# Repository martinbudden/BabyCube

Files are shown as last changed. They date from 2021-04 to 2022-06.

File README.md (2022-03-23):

# BabyCube

The **BabyCube** is a small 3D-printed CoreXY 3D printer with a linear rails motion system.

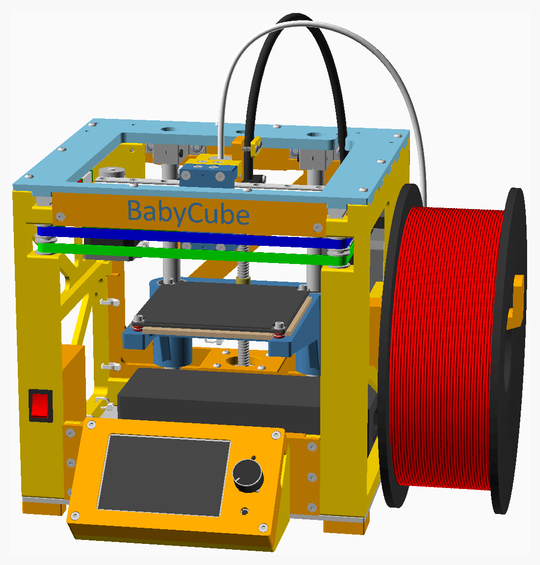
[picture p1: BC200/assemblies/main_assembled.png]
Main Assembly


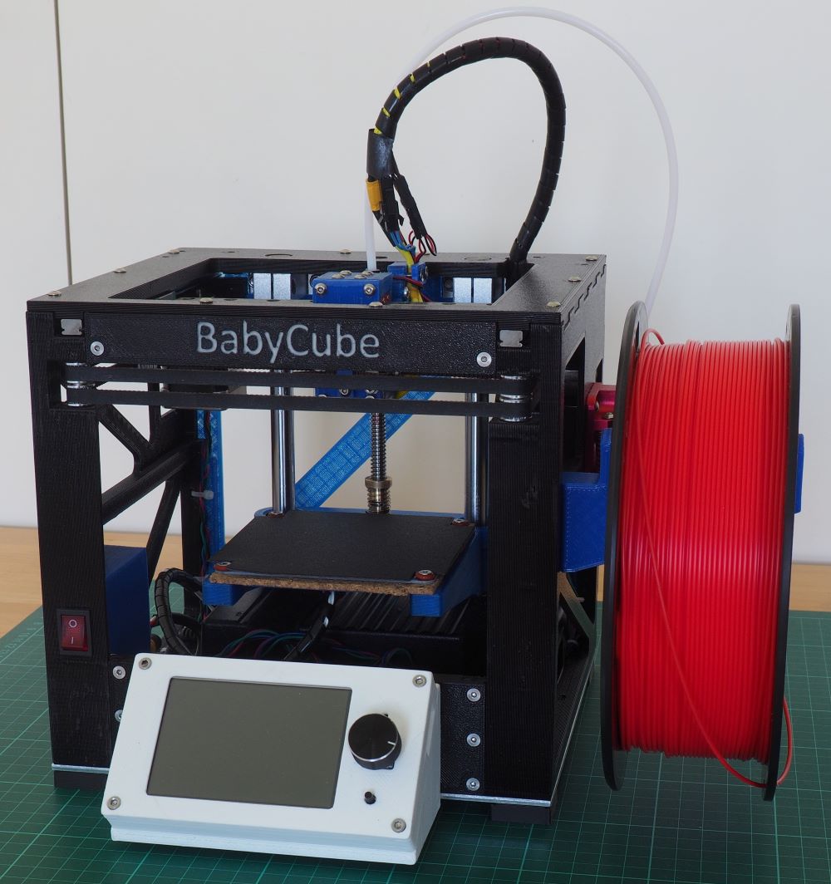
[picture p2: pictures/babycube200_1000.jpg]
BabyCube


The BabyCube has a print volume of just over 90mm by 80mm by 60mm.

The BOM cost is approximately £290 with a genuine E3D hotend (or about £250 with a generic E3D compatible hotend), this does not include the cost of filament for printing parts, see [spreadsheet](documents/BabyCube200_BOM.ods). Price is current for May 2021.

The dimensions of the cube are 220mm by 204mm by 203mm, and the enclosing volume (including the display, extruder,
and feet, but excluding the spool holder, Bowden tube and hotend wiring) is about 248mm by 272mm by 211mm.

Although the BabyCube is small and has a 3D printed frame, it is not a toy. It is an engineered machine capable of producing high quality prints.

## Assembly instructions

The assembly instructions and the BOM (parts list) are [here](BC200/readme.md). Please read all the build instructions before you begin assembly.

The STL files are on [thingiverse](https://www.thingiverse.com/thing:4911835).

A video overview of the features of BabyCube is [here](https://www.youtube.com/watch?v=HpjnHnVyvj4).

I plan to make a series of YouTube videos giving build instructions, when I have done so I will post a link here.

If you would like to build a bigger printer, you may be interested in the BabyCube's larger sibling, the [MaybeCube](https://github.com/martinbudden/MaybeCube)

## Key Features

1. Small portable quality CoreXY 3D printer with all parts integrated inside the frame (no external power brick)
2. Capable of printing high quality prints
3. Linear rails and NEMA 14 stepper motors used for CoreXY motion system
4. NEMA 17 stepper motors used for the extruder and the Z axis
5. Quiet operation
6. Sensorless homing on all axes

## Design Goals

The primary design goal was to produce a small 3D printer with a printable frame, external dimensions of approximately
200mm by 200mm by 200mm, and a target print volume of approximately 75mm by 75mm by 75mm.

The aim was that BabyCube could be printed on "standard" size printers, that is printers with a bed size of approximately 220mm by 220mm, such as the Ender 3 (print volume 220mm by 220mm by 250mm) and the Prusa i3 (print volume 250mm by 210mm by 210mm).

I printed my BabyCube on a BIQU B1 (which is similar to an Ender 3).

Further design goals:

1. **Make a 3D printer capable of producing high quality parts**
    * Ensure that the frame, even though 3D printed, is highly rigid
    * Use high quality components, including hotend, extruder, control boards etc
2. **Integrated design, with everything is enclosed within the printer's frame**
    * This includes the motors, the motion system, the power supply, and the circuit boards. The only exceptions are the extruder, the spool holder, the display and the connections to the hotend (wiring and Bowden tube).
    * all protrusions from frame (filament spool, extruder, power connector) are on the right hand side to minimise desk clutter and allow the back of the BabyCube to be pushed right against a wall
    * Clean wiring. Include the wiring in the design, rather than add it as an afterthought.
3. **Require minimal tools for assembly**
    * Assembly can essentially be completed using just hex keys.
    * Use self tapping holes rather than threaded inserts, they are just as strong - see [CNC Kitchen's video](https://www.youtube.com/watch?v=iR6OBlSzp7I)
    * Some small files are useful cleaning up printed parts, and optionally an M3 tap (and tap wrench) can be used to start self-tapping holes.
    * A drill with 2mm and 3mm bits is required to drill the holes in the aluminium base, but a 3D printed base can be used instead.
4. **Require minimal rework of printed parts**
    * [NopSCADlib](https://github.com/nophead/NopSCADlib) provides several features to avoid part rework.
    * All parts can be printed without supports. [Hanging holes](https://hydraraptor.blogspot.com/2014/03/buried-nuts-and-hanging-holes.html) are used to avoid supports in the display housing and the X_Carriage front.
    * Bolt holes are created using [horizontal holes](https://hydraraptor.blogspot.com/2020/07/horiholes-2.html) and [polyholes](https://hydraraptor.blogspot.com/2011/02/polyholes.html) and so are correct size and should not need redrilling.
5. **Use linear rails for the x and y axes**
    * linear rails are now not much more expensive than linear rods
    * linear rails make design and assembly easier, reducing the need for custom printed parts
    * linear rails allow a more compact design than linear rods
    * linear rods are used for the z-axis, since linear rails offer no advantage here
6. **Make the BabyCube as silent a possible**
    * Use TMC 2209 silent stepper drivers
    * The hotend fan is temperature regulated and only switches on when the hotend reaches 50&deg; Celsius
    * The the control board and stepper drivers are passively cooled by being thermally connected to the aluminium base (if either the BTT SKR E3 mini V2 or the BTT E3 turbo control boards are used).
    * The PSU is a fanless "brick" style laptop PSU.
7. **Try and keep the costs down**
    * the aim is not to be as cheap as possible, but rather to avoid unnecessary costs
    * use standard parts as far as possible
8. **Enable a variant with a carbon fiber frame**
    * see proof of concept [here](concepts/readme.md) (still a work in progress)
9. **Facilitate customisation and experimentation**
    * Open source design
    * Parametric design in [OpenSCAD](https://openscad.org/)
    * As far as possible, make it easy to partially disassemble the frame and exchange parts
10. **Support different size and material variants**
    * BabyCube's parametric design allows different size variants
11. **Be delightful**
    * A good design should have aspects that the user finds delightful

## Variants

The standard variant of the BabyCube uses and OpenBuilds 100 x 100 mm heated bed, however it is also possible to use a 120 x 120 x 6 mm aluminium tooling plate with a heating pad, see [printbed 120](PRINTBED120/readme.md).

The standard variant uses a BigTreeTech SKR Mini E3 v2.0 controller, however it is also possible to use the BigTreeTech SKR v1.4 (and Turbo) and BigTreeTech E3 Turbo controllers.

The standard variant uses an E3D v6 hotend, but other groovemount based hotends could be used.

The standard variant uses a BigTreeTech TFT35 v3.0 display, however it should also be possible to produce "headless" variants:

* if you use the SKR v1.4 or the SKR E3 turbo controller you can install the RepRap firmware and dispense with the display.
* you can install Klipper firmware and use a Raspberry Pi.

I have started to look at developing a variant with a carbon fiber frame, however this is very much a [work in progress](concepts/readme.md).

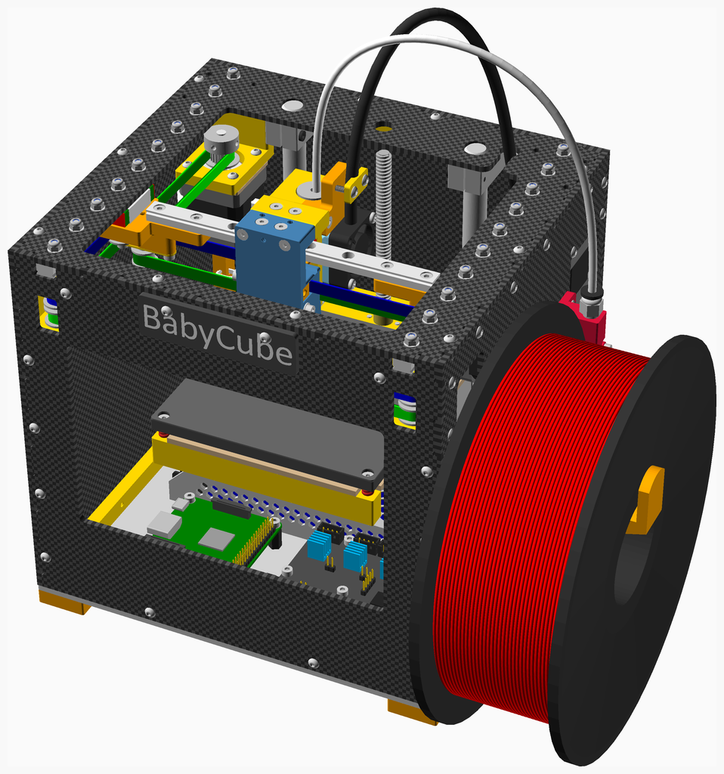
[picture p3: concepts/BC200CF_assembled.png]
BabyCubeCF


The exploded version:

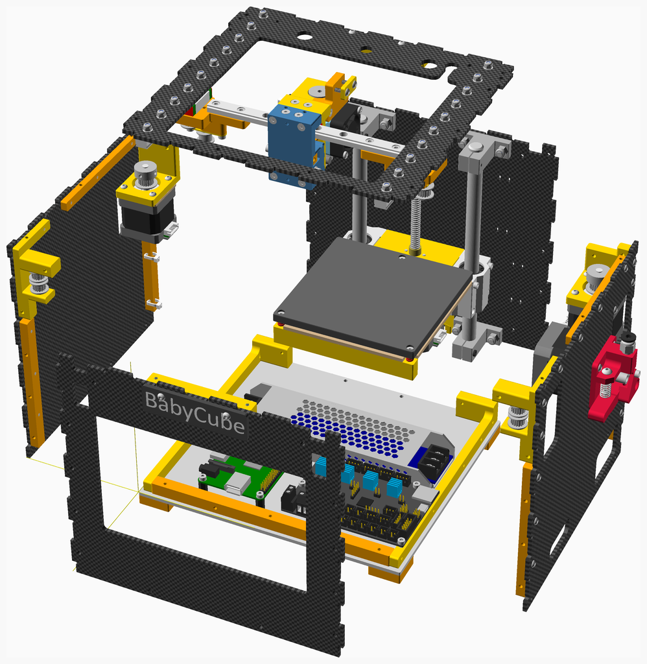
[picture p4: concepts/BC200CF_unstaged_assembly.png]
BabyCubeCF exploded


## Comparisons

The following table compares the sizes and build volumes of various small 3D printers.

Printer           | Build Volume | Nominal Dimensions
------------------| -------------| -------------------
BabyCube          | 90 x 80 x 60 | 200 x 220 x 210
[Dice](https://www.instructables.com/DICE-a-Tiny-Rigid-and-Superfast-3D-printer/) | 90 x 75 x 80  | 200 x 200 x 200
[Voron 0](https://vorondesign.com/voron0) | 120 x 120 x 120 | 230 x 230 x 280

## Demo videos

| | Overview | SpeedBoatRace |
| ----- | :---: | :---: |
| Video | Overview (https://www.youtube.com/watch?v=HpjnHnVyvj4) | Speed benchy (https://www.youtube.com/watch?v=jGo57FBjNX4) |

## Input shaper test results

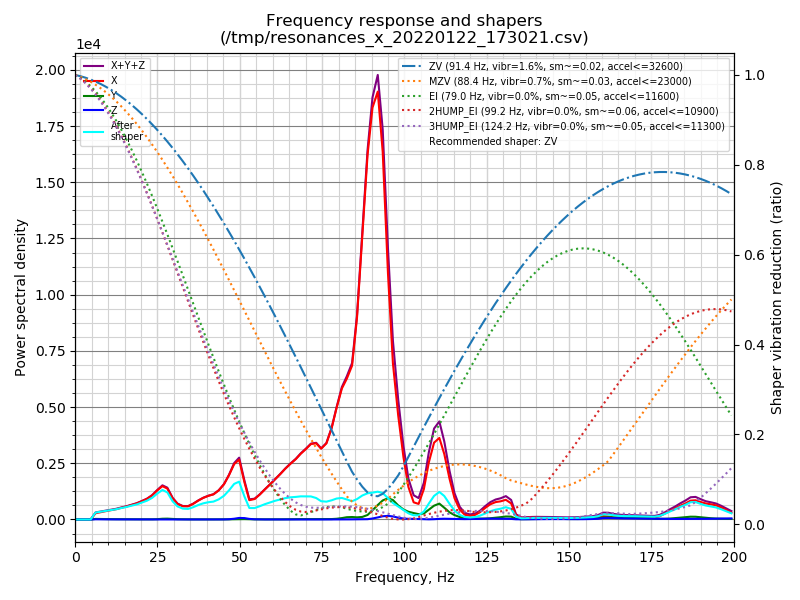
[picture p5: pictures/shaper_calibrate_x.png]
X-Axis

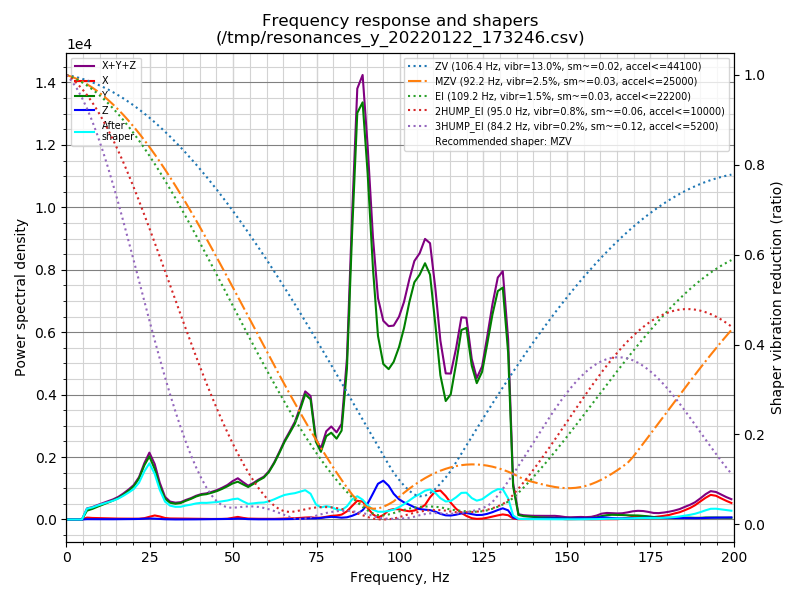
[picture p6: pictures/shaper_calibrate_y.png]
Y-Axis


## Pictures

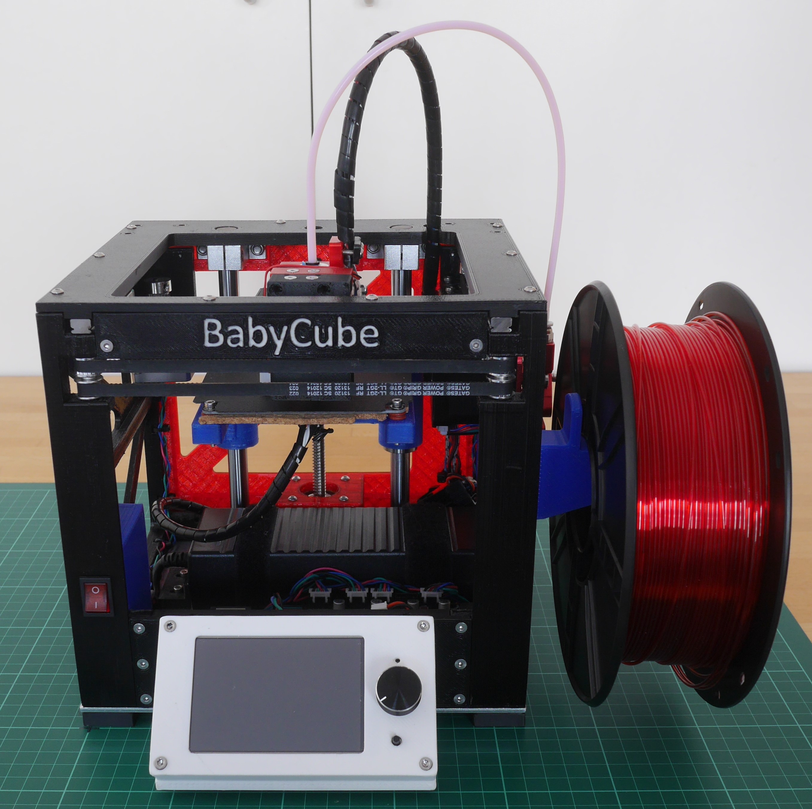
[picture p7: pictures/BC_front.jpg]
Front

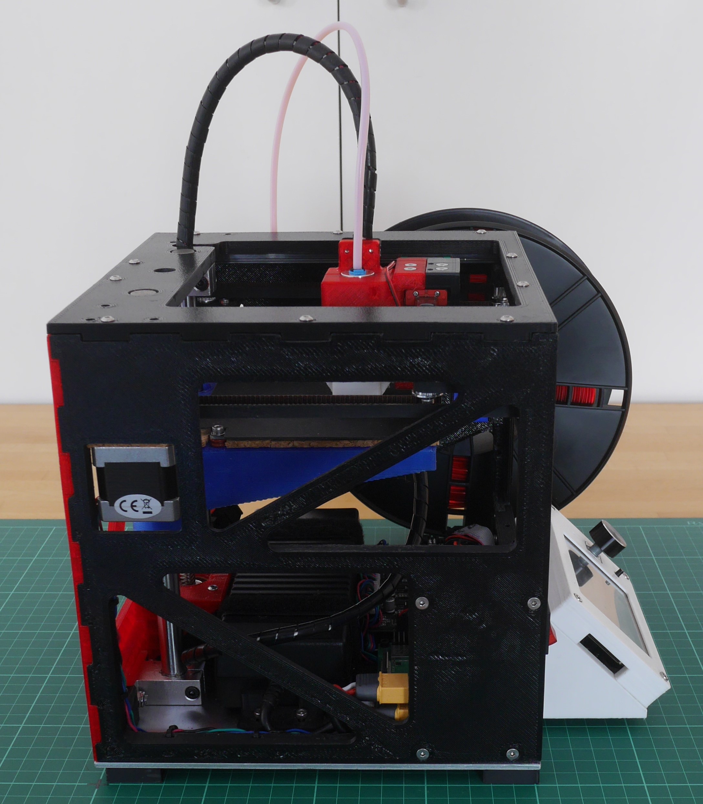
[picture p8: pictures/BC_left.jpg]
Left

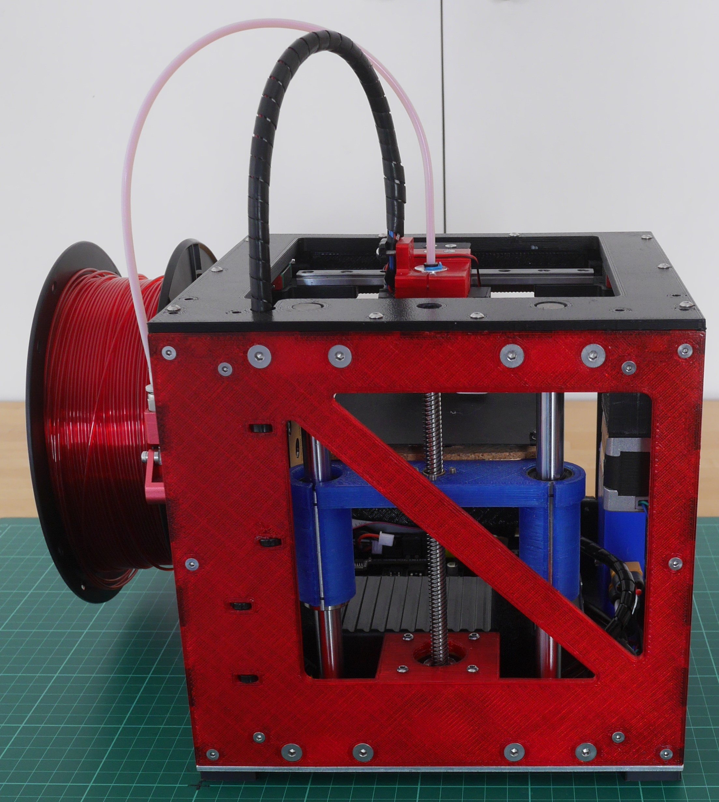
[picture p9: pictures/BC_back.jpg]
Back

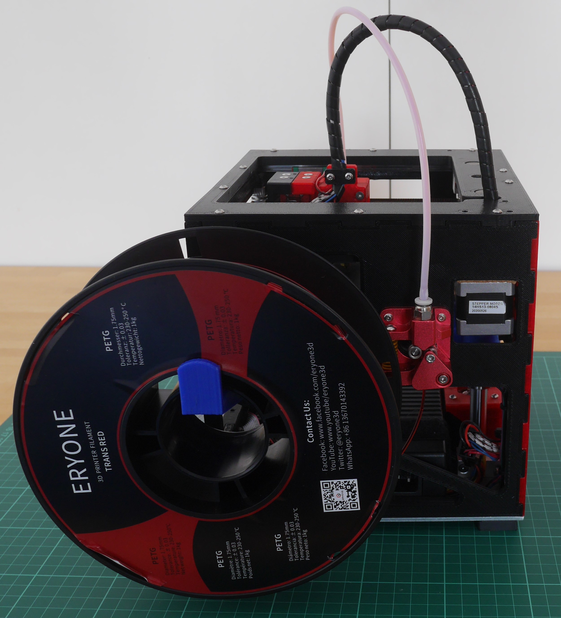
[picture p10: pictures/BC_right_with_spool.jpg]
Right with spool

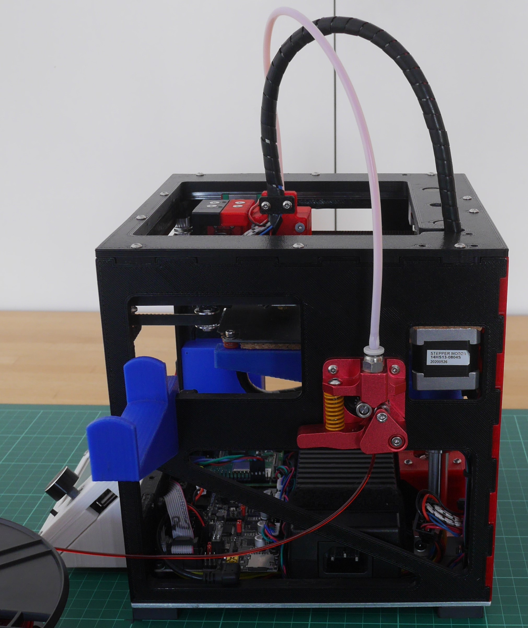
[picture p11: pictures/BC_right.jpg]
Right

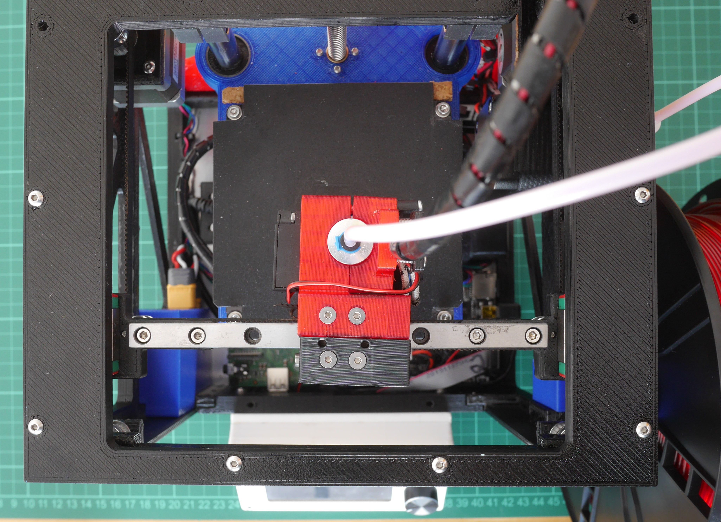
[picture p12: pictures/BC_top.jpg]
Top

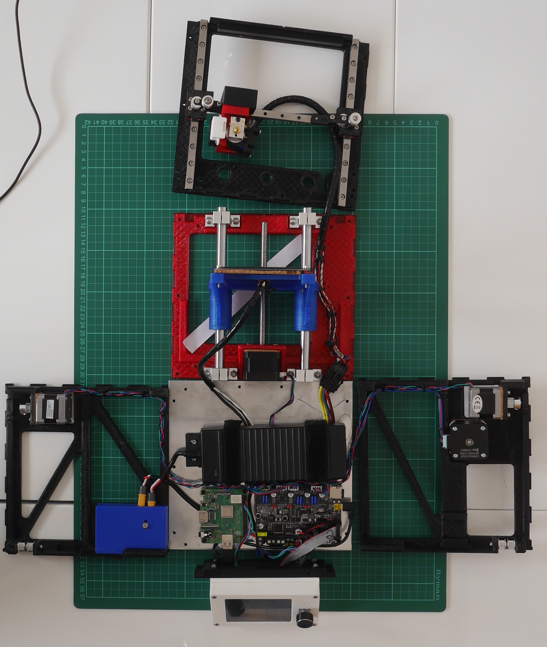
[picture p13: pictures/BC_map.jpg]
Map


## License

BabyCube is licensed under the [Creative Commons Attribution-NonCommercial-ShareAlike 4.0 International License](https://creativecommons.org/licenses/by-nc-sa/4.0/)
(CC BY-NC-SA 4.0)<br />
<a rel="license" href="http://creativecommons.org/licenses/by-nc-sa/4.0/">

</a>

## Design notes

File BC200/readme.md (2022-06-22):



# BabyCube Assembly Instructions

These are the assembly instructions for the BabyCube. These instructions are not fully comprehensive, that is they do
not show every small detail of the construction, and in particular they do not show the wiring. However there is sufficient
detail that someone with a good understanding of 3D printers can build the BabyCube.

Main Assembly

BabyCube

<span></span>

---

## Table of Contents

1. [Parts list](#Parts_list)
1. [Printhead_E3DV6_MGN9C assembly](#Printhead_E3DV6_MGN9C_assembly)
1. [X_Carriage_Belt_Side_MGN9C assembly](#X_Carriage_Belt_Side_MGN9C_assembly)
1. [Top_Face_Stage_1 assembly](#Top_Face_Stage_1_assembly)
1. [Top_Face_Stage_2 assembly](#Top_Face_Stage_2_assembly)
1. [Top_Face assembly](#Top_Face_assembly)
1. [Display_Cover assembly](#Display_Cover_assembly)
1. [Display_Housing assembly](#Display_Housing_assembly)
1. [Z_Carriage assembly](#Z_Carriage_assembly)
1. [Print_bed assembly](#Print_bed_assembly)
1. [Back_Face_Stage_1 assembly](#Back_Face_Stage_1_assembly)
1. [Back_Face assembly](#Back_Face_assembly)
1. [Right_Face_Stage_1 assembly](#Right_Face_Stage_1_assembly)
1. [Right_Face assembly](#Right_Face_assembly)
1. [Base assembly](#Base_assembly)
1. [Switch_Shroud assembly](#Switch_Shroud_assembly)
1. [Left_Face assembly](#Left_Face_assembly)
1. [Stage_1 assembly](#Stage_1_assembly)
1. [Stage_2 assembly](#Stage_2_assembly)
1. [Stage_3 assembly](#Stage_3_assembly)
1. [Stage_4 assembly](#Stage_4_assembly)
1. [Stage_5 assembly](#Stage_5_assembly)
1. [Main assembly](#main_assembly)

## Tips for printing the parts

The printed parts can be divided into two classes, the "large parts" (ie the left, right, top and back faces), and the
"small parts" (the rest of the parts)

I recommend using a 0.6mm nozzle for printing all the parts, but especially the for the large parts.

### Parts in proximity to heat sources

A number of parts are in proximity with heat sources, namely the hotend, the heated bed and the motors. Ideally these
should be printed in ABS, but I have used successfully used PETG.  These parts are insulated from direct contact with
the heat sources, by O-rings and cork underlay (for the heated bed) and by cork dampers (for the motors). These
insulators should not be omitted from the build.

### Small parts

For dimensional accuracy the small parts need to be printed with a layer height of 0.25mm and a first layer height of 0.25mm.
To maximise part strength, I use the following:

1. extrusion width of 0.7mm if using a 0.6mm nozzle, 0.65mm if using a 0.4mm nozzle
2. 3 perimeters
3. 3 top and bottom layers
4. Grid (or honeycomb) infill - not any of the weaker infills (eg Rectangular). 30% infill.

### Large parts

For the large parts, I use a 0.6mm nozzle with the following settings:

1. Layer height 0.5mm, same for first layer height
2. Extrusion width of 1.0mm
3. 2 perimeters (only 2 needed because of the 1.0mm extrusion width)
4. 2 bottom layers (only 2 needed because of the 0.5mm layer height)
5. 3 top layers (3 needed because the first layer may be in some parts a bridging layer and so is not full strength,
the second and third layers are structural layers).
6. Grid infill at 30%. I find that honeycomb infill, although stronger, is more prone to warping. 30% is used to enable
the part cooling fan to be switched off (see tips below).
7. First layer speed 25mm/s
8. If using a standard E3D v6 hotend (ie not a Volcano or other high-volume hotend) set the max volumetric speed to
14mm<sup>3</sup>/s for PLA, 11mm<sup>3</sup>/s for ABS, or 8mm<sup>3</sup>/s for PETG

The large parts take up almost the full extent of the print bed and as a result can be prone to warping.
If you have problems with warping, I suggest the following:

1. disable the part cooling fan for the first 10mm (20 layers) or more. The part cooling fan is only really required
for the bridges for the motor mounts and switch mounts, since there are no overhangs and the small bolt holes bridge
fine without part cooling.
2. raise the temperature of the heated bed.
3. add a brim

## Part substitutions

There is some scope for part substitution:

1. Generally caphead bolts can be used instead of button head bolts, except on the print head where caphead bolts may interfere
with homing.
2. I strongly recommend using an aluminium baseplate, but if you have difficulty sourcing this, or cutting it to size, a
3D printed baseplate can be used instead.

## Configuring the printer

There are a number of features that are important to consider when configuring the printer.

### Sensorless homing

Configuring sensorless homing on the X and Y axes is done in the standard way. Sensorless homing on the Z-axis must
be set up to home at the bottom of the Z-axis - so that homing does not cause the print head to crash into the print
bed.

### Power management

The steady state power usage of the BabyCube during printing is about 40W, well within the capabilities of the 120W
power supply. However peak power usage must be managed so as not to exceed 120W.

1. Use PID temperature control (not bang-bang) for the heated bed. In Marlin this means defining `PIDTEMPBED` in
`configuration.h`
2. In the printer start gcode in your slicer, do not set all the heating going at once, instead use a phased approach
   1. Use `M104 S160` to start the hotend heating without waiting
   2. Home the Y axis (note Y axis should be homed before X axis to avoid possible printhead collision with sides)
   3. Home the X axis
   4. Home the Z axis
   5. Use `M400` to wait for the motors to stop
   6. Use `M140 S{first_layer_bed_temperature[0]}` to set the first layer bed temperature
   7. Use `M109 S{first_layer_temperature[0]}` to set the temperature for nozzle 0 and wait

This avoids having all the motors and both heaters on during startup. Once the hotend and heated bed have warmed up,
their power usage decreases (since they use PID controllers, and power usage is (mostly) proportional (that's the P in
PID) to the difference between the actual heater temperature and the target temperature).

Example printer start gcode for Slic3r/PrusaSlicer/SuperSlicer is [here](../../documents/PrinterStart.gcode).
Example printer end gcode for is [here](../../documents/PrinterEnd.gcode).

### Fans

The power supply is 19.5V and the fans specified are 12V. This is handled by setting `FAN_MAX_PWM` to `157` and
`EXTRUDER_AUTO_FAN_SPEED` to `150` in `configuration_adv.h`. (`12/19.5*255 = 157`, so setting these values to 157 or
less ensures the fans' voltage specification is not exceeded.)

### Marlin configuration

The changes to `configuration.h` and `configuration_adv.h` are [here](../../documents/MarlinConfiguration.md).

<span></span>
[Top](#TOP)

---

## Parts list

| <span style="writing-mode: vertical-rl; text-orientation: mixed;">Printhead E3DV6 MGN9C</span> | <span style="writing-mode: vertical-rl; text-orientation: mixed;">X Carriage Belt Side MGN9C</span> | <span style="writing-mode: vertical-rl; text-orientation: mixed;">Top Face</span> | <span style="writing-mode: vertical-rl; text-orientation: mixed;">Display Housing</span> | <span style="writing-mode: vertical-rl; text-orientation: mixed;">Print Bed</span> | <span style="writing-mode: vertical-rl; text-orientation: mixed;">Back Face</span> | <span style="writing-mode: vertical-rl; text-orientation: mixed;">Right Face</span> | <span style="writing-mode: vertical-rl; text-orientation: mixed;">Base</span> | <span style="writing-mode: vertical-rl; text-orientation: mixed;">Left Face</span> | <span style="writing-mode: vertical-rl; text-orientation: mixed;">Main</span> | <span style="writing-mode: vertical-rl; text-orientation: mixed;">TOTALS</span> |  |
|-----:|-----:|-----:|-----:|-----:|-----:|-----:|-----:|-----:|-----:|---:|:---|
| | | | | | | | | | | | **Vitamins** |
| .  | .  | .  | .  | .  | .  | .  | 1  | .  | .  | 1  |  Aluminium box section 12mm x 8mm x 1mm, length 85mm |
| .  | .  | .  | .  | .  | .  | .  | 1  | .  | .  | 1  |  Aluminium sheet 220mm x 204mm x 3mm |
| .  | .  | .  | .  | .  | .  | .  | .  | .  | 1  | 1  |  Belt GT2 x 6mm x 728mm |
| .  | .  | .  | .  | .  | .  | .  | .  | .  | 1  | 1  |  Belt GT2 x 6mm x 728mm |
| .  | .  | .  | .  | .  | .  | .  | 1  | .  | .  | 1  |  BigTreeTech SKR Mini E3 v2.0 |
| .  | .  | .  | 1  | .  | .  | .  | .  | .  | .  | 1  |  BigTreeTech TFT35 v3.0 |
| 4  | .  | .  | .  | .  | .  | .  | .  | .  | .  | 4  |  Bolt M2 caphead x  6mm |
| .  | .  | .  | .  | .  | .  | .  | .  | .  | 2  | 2  |  Bolt M3 buttonhead x  8mm |
| .  | .  | .  | .  | .  | .  | .  | 2  | 1  | 4  | 7  |  Bolt M3 buttonhead x 10mm |
| 2  | .  | .  | .  | .  | 4  | 4  | .  | 4  |  18  | 32  |  Bolt M3 buttonhead x 12mm |
| .  | .  | .  | 4  | .  | .  | .  | .  | .  | .  | 4  |  Bolt M3 buttonhead x 16mm |
| .  | .  | .  | 4  | .  | .  | .  | 4  | .  | .  | 8  |  Bolt M3 caphead x  6mm |
| .  | .  |  26  | .  | 4  | .  | .  |  14  | .  | .  | 44  |  Bolt M3 caphead x  8mm |
| .  | .  | 6  | .  | .  | .  | .  | .  | .  | .  | 6  |  Bolt M3 caphead x 10mm |
| .  | .  | 2  | 4  | 4  | .  | .  | .  | .  | .  | 10  |  Bolt M3 caphead x 16mm |
| .  | .  | 2  | .  | .  | .  | .  | .  | .  | .  | 2  |  Bolt M3 caphead x 25mm |
| .  | 2  | .  | .  | .  | .  | .  | .  | .  | .  | 2  |  Bolt M3 caphead x 30mm |
| .  | .  | .  | .  | .  | .  | .  | .  | .  | 6  | 6  |  Bolt M3 countersunk x  6mm |
| .  | .  | 2  | .  | .  | .  | .  | .  | .  |  14  | 16  |  Bolt M3 countersunk x 10mm |
| .  | .  | .  | .  | .  | .  | .  | .  | 2  | 4  | 6  |  Bolt M3 countersunk x 12mm |
| .  | .  | .  | .  | .  | .  | .  | .  | 2  | .  | 2  |  Bolt M3 countersunk x 16mm |
| 2  | .  | .  | .  | .  | .  | .  | .  | .  | .  | 2  |  Bolt M3 countersunk x 25mm |
| .  | .  | .  | .  | .  | .  | .  | .  | .  | 4  | 4  |  Bolt M3 countersunk x 30mm |
| .  | .  | .  | .  | .  | .  | 1  | .  | 1  | .  | 2  |  Bolt M3 countersunk x 35mm |
| .  | .  | .  | .  | .  | 8  | .  | .  | .  | .  | 8  |  Bolt M5 countersunk x 16mm |
| .  | .  | .  | .  | .  | .  | 1  | .  | 1  | .  | 2  |  Cork damper NEMA 14 |
| .  | .  | .  | .  | .  | 1  | 1  | .  | .  | .  | 2  |  Cork damper NEMA 17 |
| .  | .  | .  | .  | 1  | .  | .  | .  | .  | .  | 1  |  Cork underlay 105mm x 105mm x 3mm |
| 1  | .  | .  | .  | .  | .  | .  | .  | .  | .  | 1  |  Fan 30mm x 10mm |
| 1  | .  | .  | .  | .  | .  | .  | .  | .  | .  | 1  |  Hot end E3D V6 direct 1.75mm |
| .  | .  | .  | .  | .  | 1  | .  | .  | .  | .  | 1  |  Leadscrew 8mm x 150mm |
| .  | .  | .  | .  | 1  | .  | .  | .  | .  | .  | 1  |  Leadscrew nut 8 x 2 |
| .  | .  | .  | .  | 2  | .  | .  | .  | .  | .  | 2  |  Linear bearing LM12LUU |
| .  | .  | 1  | .  | .  | .  | .  | .  | .  | .  | 1  |  Linear rail MGN9 x 150mm |
| .  | .  | 2  | .  | .  | .  | .  | .  | .  | .  | 2  |  Linear rail MGN9 x 200mm |
| .  | .  | 3  | .  | .  | .  | .  | .  | .  | .  | 3  |  Linear rail carriage MGN9C |
| .  | .  | .  | .  | .  | 2  | .  | .  | .  | .  | 2  |  Linear rod 12mm x 200mm |
| .  | .  | .  | .  | .  | .  | 1  | .  | .  | .  | 1  |  MK10 Dual Pulley Extruder |
| .  | .  | .  | .  | 1  | .  | .  | .  | .  | .  | 1  |  Magnetic base 100mm x 100mm |
| .  | .  | .  | .  | .  | .  | .  | 1  | .  | .  | 1  |  Micro SD card |
| .  | .  | .  | .  | .  | 8  | .  | .  | .  | .  | 8  |  Nut M5 nyloc |
| .  | .  | .  | .  | 8  | .  | .  | .  | .  | .  | 8  |  O-ring nitrile 4mm x 2mm |
| .  | .  | .  | .  | 1  | .  | .  | .  | .  | .  | 1  |  OpenBuilds mini heated bed 100mm x 100mm |
| .  | .  | .  | .  | .  | .  | .  | .  | .  | 1  | 1  |  PTFE tube 292 mm |
| .  | .  | .  | .  | .  | .  | .  | 9  | .  | .  | 9  |  Pillar hex nylon F/F M3x12 |
| .  | .  | .  | .  | 1  | .  | .  | .  | .  | .  | 1  |  Print surface 100mm x 100mm |
| .  | .  | 2  | .  | .  | .  | 2  | .  | 2  | .  | 6  |  Pulley GT2 idler 16 teeth |
| .  | .  | 2  | .  | .  | .  | .  | .  | .  | .  | 2  |  Pulley GT2 idler smooth 9.63mm |
| .  | .  | .  | .  | .  | .  | 1  | .  | 1  | .  | 2  |  Pulley GT2UM 20 teeth |
| .  | .  | .  | .  | .  | .  | .  | 1  | .  | .  | 1  |  Raspberry Pi 3A+ |
| .  | .  | .  | .  | .  | .  | .  | .  | 1  | .  | 1  |  Rocker Switch PRASA1-16F-BB0BW |
| .  | .  | .  | .  | .  | 4  | .  | .  | .  | .  | 4  |  SK12 shaft support bracket |
| .  | .  | .  | .  | .  | .  | .  | .  | .  | 1  | 1  |  Spiral wrap, 500mm |
| 1  | .  | .  | .  | .  | .  | .  | .  | .  | .  | 1  |  Square radial fan 3010 |
| .  | .  | .  | .  | .  | .  | 1  | .  | 1  | .  | 2  |  Stepper motor NEMA14 x 36mm |
| .  | .  | .  | .  | .  | 1  | .  | .  | .  | .  | 1  |  Stepper motor NEMA17 x 34mm |
| .  | .  | .  | .  | .  | .  | 1  | .  | .  | .  | 1  |  Stepper motor NEMA17 x 40mm |
| .  | .  | .  | .  | .  | 1  | .  | .  | .  | .  | 1  |  Stepper motor cable, 150mm |
| .  | .  | .  | .  | .  | .  | 2  | .  | 1  | .  | 3  |  Stepper motor cable, 400mm |
| .  | 2  | 6  | .  | 8  | .  | 6  | .  | 6  | .  | 28  |  Washer M3 |
| .  | .  | .  | .  | .  | .  | .  | .  | 2  | .  | 2  |  Wire black 12SWG, length 100mm |
| .  | .  | .  | .  | .  | .  | .  | .  | 2  | .  | 2  |  Wire red 12SWG, length 100mm |
| .  | .  | .  | .  | .  | .  | .  | .  | 1  | .  | 1  |  XT60 Connector Female |
| .  | .  | .  | .  | .  | .  | .  | .  | 1  | .  | 1  |  XT60 Connector Female - not shown |
| .  | .  | .  | .  | .  | .  | .  | .  | 1  | .  | 1  |  XT60 Connector Male |
| .  | .  | .  | .  | .  | .  | .  | .  | 1  | .  | 1  |  XT60 Connector Male - not shown |
| 1  | .  | .  | .  | 2  | .  | 5  | .  | 4  | 4  | 16  |  Ziptie 2.5mm x 100mm min length |
|  12  | 4  |  54  |  13  |  33  |  30  |  26  |  34  |  35  |  60  |  301  | Total vitamins count |
| | | | | | | | | | | | **3D printed parts** |
| .  | .  | .  | .  | .  | 1  | .  | .  | .  | .  | 1  | Back_Face.stl |
| .  | .  | .  | .  | .  | .  | .  | 1  | .  | .  | 1  | Base.stl |
| .  | .  | .  | .  | .  | .  | .  | 1  | .  | .  | 1  | Base_Template.stl |
| .  | .  | .  | 1  | .  | .  | .  | .  | .  | .  | 1  | Display_Housing.stl |
| .  | .  | .  | 1  | .  | .  | .  | .  | .  | .  | 1  | Display_Housing_Bracket.stl |
| 1  | .  | .  | .  | .  | .  | .  | .  | .  | .  | 1  | Fan_Duct.stl |
| .  | .  | .  | .  | .  | .  | .  | .  | .  | 4  | 4  | Foot_LShaped_8mm.stl |
| .  | .  | .  | 1  | .  | .  | .  | .  | .  | .  | 1  | Front_Lower_Chord.stl |
| .  | .  | .  | .  | .  | .  | .  | .  | .  | 1  | 1  | Front_Upper_Chord.stl |
| 1  | .  | .  | .  | .  | .  | .  | .  | .  | .  | 1  | Hotend_Clamp.stl |
| 1  | .  | .  | .  | .  | .  | .  | .  | .  | .  | 1  | Hotend_Strain_Relief_Clamp.stl |
| .  | .  | .  | .  | .  | .  | .  | .  | 1  | .  | 1  | Left_Face.stl |
| .  | .  | .  | .  | .  | .  | .  | 1  | .  | .  | 1  | PSU_Bracket.stl |
| .  | .  | .  | .  | .  | .  | .  | 2  | .  | .  | 2  | PSU_Support.stl |
| .  | .  | .  | .  | .  | .  | 1  | .  | .  | .  | 1  | Right_Face.stl |
| .  | .  | .  | .  | .  | .  | .  | .  | .  | 1  | 1  | Spool_Holder.stl |
| .  | .  | .  | .  | .  | .  | .  | .  | 1  | .  | 1  | Switch_Shroud.stl |
| .  | .  | .  | .  | .  | .  | .  | .  | 1  | .  | 1  | Switch_Shroud_Clamp.stl |
| .  | .  | 1  | .  | .  | .  | .  | .  | .  | .  | 1  | Top_Face.stl |
| .  | .  | .  | .  | .  | .  | .  | .  | .  | 1  | 1  | X_Carriage_Belt_Clamp.stl |
| .  | 1  | .  | .  | .  | .  | .  | .  | .  | .  | 1  | X_Carriage_Belt_Side_MGN9C.stl |
| .  | 2  | .  | .  | .  | .  | .  | .  | .  | .  | 2  | X_Carriage_Belt_Tensioner.stl |
| 1  | .  | .  | .  | .  | .  | .  | .  | .  | .  | 1  | X_Carriage_Groovemount_MGN9C.stl |
| .  | .  | 1  | .  | .  | .  | .  | .  | .  | .  | 1  | Y_Carriage_Brace_Left.stl |
| .  | .  | 1  | .  | .  | .  | .  | .  | .  | .  | 1  | Y_Carriage_Brace_Right.stl |
| .  | .  | 1  | .  | .  | .  | .  | .  | .  | .  | 1  | Y_Carriage_Left.stl |
| .  | .  | 1  | .  | .  | .  | .  | .  | .  | .  | 1  | Y_Carriage_Right.stl |
| .  | .  | .  | .  | 1  | .  | .  | .  | .  | .  | 1  | Z_Carriage.stl |
| 4  | 3  | 5  | 3  | 1  | 1  | 1  | 5  | 3  | 7  | 33  | Total 3D printed parts count |
| | | | | | | | | | | | **CNC routed parts** |
| .  | .  | .  | .  | .  | .  | .  | 1  | .  | .  | 1  | BaseAL.dxf |
| .  | .  | .  | .  | .  | .  | .  | 1  | .  | .  | 1  | Total CNC routed parts count |

<span></span>
[Top](#TOP)

---

## Printhead_E3DV6_MGN9C assembly

### Vitamins

| Qty | Description |
|----:|:---|
| 4 | Bolt M2 caphead x  6mm |
| 2 | Bolt M3 buttonhead x 12mm |
| 2 | Bolt M3 countersunk x 25mm |
| 1 | Fan 30mm x 10mm |
| 1 | Hot end E3D V6 direct 1.75mm |
| 1 | Square radial fan 3010 |
| 1 | Ziptie 2.5mm x 100mm min length |

### 3D Printed parts

| 1 x Fan_Duct.stl | 1 x Hotend_Clamp.stl | 1 x Hotend_Strain_Relief_Clamp.stl |
|---|---|---|
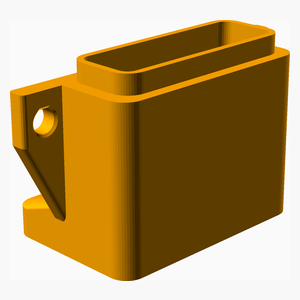
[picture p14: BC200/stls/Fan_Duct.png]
Fan_Duct.stl
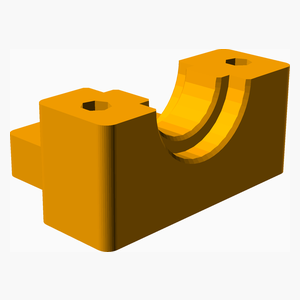
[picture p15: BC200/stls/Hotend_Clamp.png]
Hotend_Clamp.stl
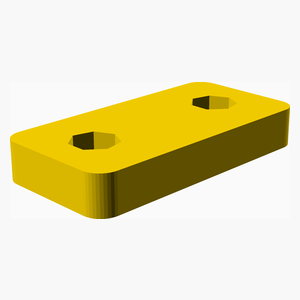
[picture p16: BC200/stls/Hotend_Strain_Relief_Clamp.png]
Hotend_Strain_Relief_Clamp.stl
|  |  |  |
| 1 x X_Carriage_Groovemount_MGN9C.stl |
|----------|
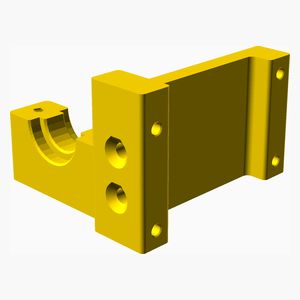
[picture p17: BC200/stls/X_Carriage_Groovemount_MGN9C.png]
X_Carriage_Groovemount_MGN9C.stl
|  |

### Assembly instructions

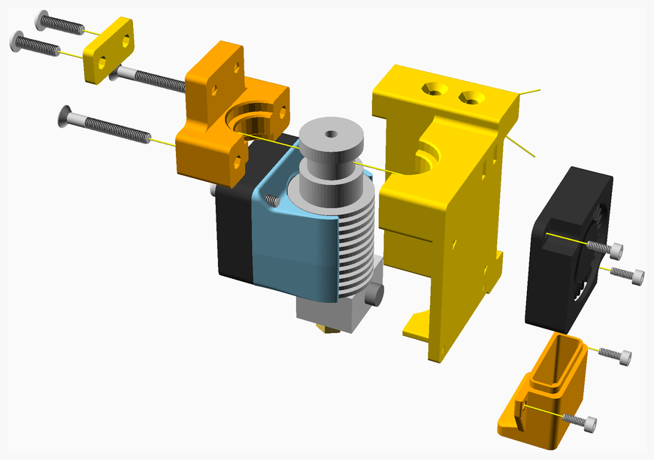
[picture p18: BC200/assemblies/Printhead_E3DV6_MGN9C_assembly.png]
Printhead_E3DV6_MGN9C_assembly


1. Assemble the E3D hotend, including fan, thermistor cartridge and heater cartridge.
2. Use the **Hotend_Clamp** to attach the hotend to the **X_Carriage**.
3. Collect the wires together and attach to the **X_Carriage** using the **Hotend_Strain_Relief_Clamp**.

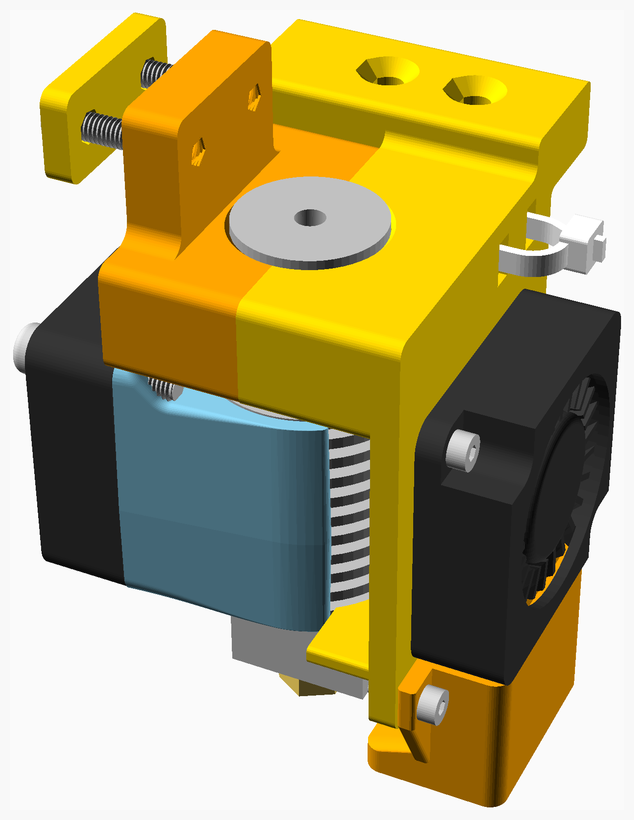
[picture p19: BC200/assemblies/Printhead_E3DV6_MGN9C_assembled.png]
Printhead_E3DV6_MGN9C_assembled


<span></span>
[Top](#TOP)

---

## X_Carriage_Belt_Side_MGN9C assembly

### Vitamins

| Qty | Description |
|----:|:---|
| 2 | Bolt M3 caphead x 30mm |
| 2 | Washer M3 |

### 3D Printed parts

| 1 x X_Carriage_Belt_Side_MGN9C.stl | 2 x X_Carriage_Belt_Tensioner.stl |
|---|---|
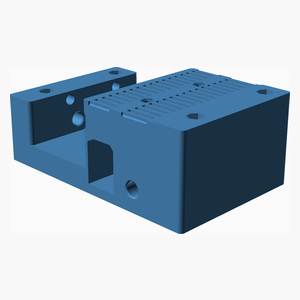
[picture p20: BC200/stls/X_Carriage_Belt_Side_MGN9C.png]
X_Carriage_Belt_Side_MGN9C.stl
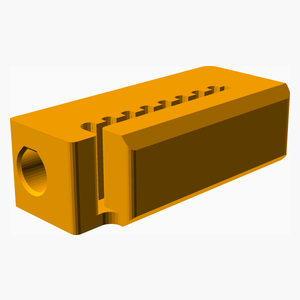
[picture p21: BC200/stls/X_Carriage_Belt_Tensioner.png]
X_Carriage_Belt_Tensioner.stl
|  |  |

### Assembly instructions

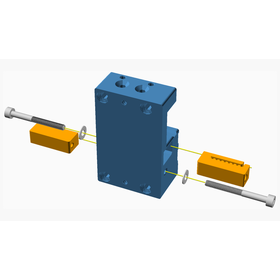
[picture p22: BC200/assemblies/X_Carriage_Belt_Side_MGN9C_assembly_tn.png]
X_Carriage_Belt_Side_MGN9C_assembly


Insert the belts into the **X_Carriage_Belt_Tensioner**s and then bolt the tensioners into the
**X_Carriage_Belt_Side_MGN9C** part as shown. Note the belts are not shown in this diagram.

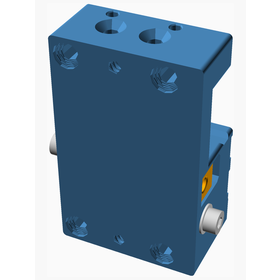
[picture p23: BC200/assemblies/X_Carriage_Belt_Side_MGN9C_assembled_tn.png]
X_Carriage_Belt_Side_MGN9C_assembled


<span></span>
[Top](#TOP)

---

## Top_Face_Stage_1 assembly

### Vitamins

| Qty | Description |
|----:|:---|
|  18 | Bolt M3 caphead x  8mm |
| 2 | Bolt M3 countersunk x 10mm |
| 2 | Linear rail MGN9 x 200mm |
| 2 | Linear rail carriage MGN9C |

### 3D Printed parts

| 1 x Top_Face.stl |
|----------|
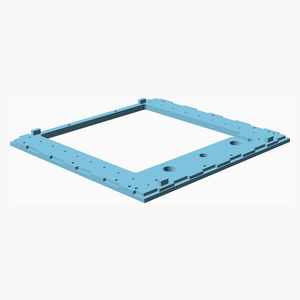
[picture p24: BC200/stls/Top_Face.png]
Top_Face.stl
|  |

### Assembly instructions

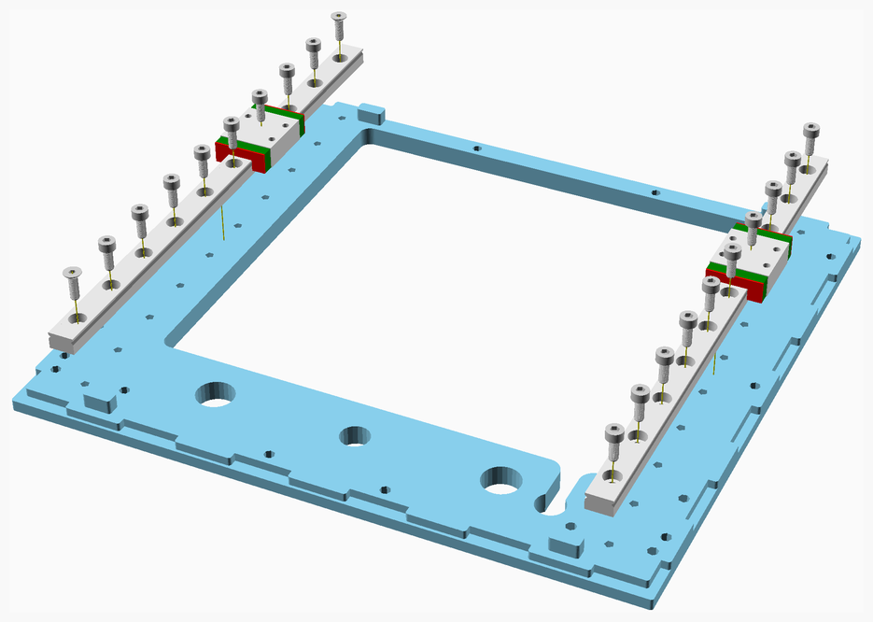
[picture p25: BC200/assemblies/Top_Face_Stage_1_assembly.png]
Top_Face_Stage_1_assembly


1. Turn the **Top_Face** upside down and place it on a flat surface.
2. Bolt the rails to the **Top_Face**. Note that the first and last bolts on the left rail are countersunk bolts and act
as pilot bolts to ensure the rails are aligned precisely - they should be tightened before all the other bolts on the
left side.
3. The bolts on the right side rail should be only loosely tightened - they will be fully tightened when the right rail
is aligned when the X axis rail is added.

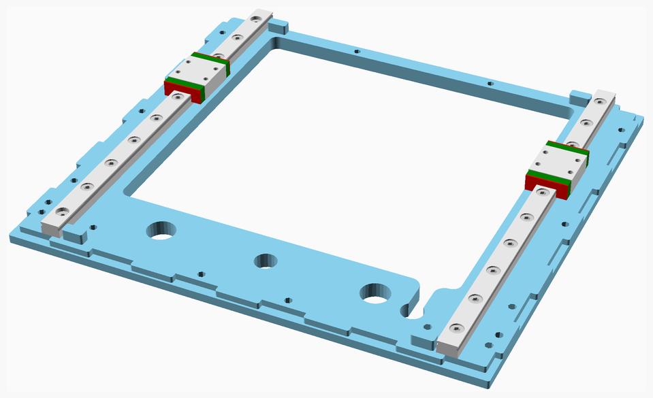
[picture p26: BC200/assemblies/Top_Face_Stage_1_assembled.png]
Top_Face_Stage_1_assembled


<span></span>
[Top](#TOP)

---

## Top_Face_Stage_2 assembly

### Vitamins

| Qty | Description |
|----:|:---|
| 8 | Bolt M3 caphead x  8mm |
| 2 | Bolt M3 caphead x 10mm |
| 2 | Bolt M3 caphead x 16mm |
| 2 | Bolt M3 caphead x 25mm |
| 2 | Pulley GT2 idler 16 teeth |
| 2 | Pulley GT2 idler smooth 9.63mm |
| 6 | Washer M3 |

### 3D Printed parts

| 1 x Y_Carriage_Brace_Left.stl | 1 x Y_Carriage_Brace_Right.stl | 1 x Y_Carriage_Left.stl |
|---|---|---|
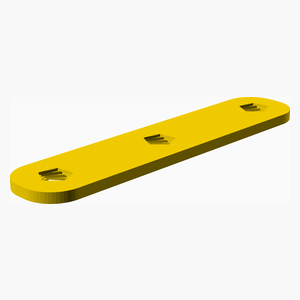
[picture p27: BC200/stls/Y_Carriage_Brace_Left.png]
Y_Carriage_Brace_Left.stl
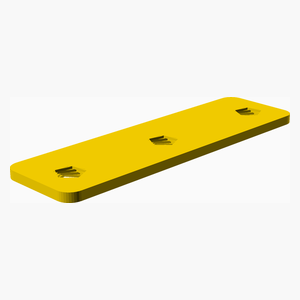
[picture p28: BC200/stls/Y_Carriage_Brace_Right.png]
Y_Carriage_Brace_Right.stl
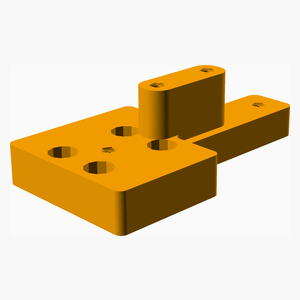
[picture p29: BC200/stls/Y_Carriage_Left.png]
Y_Carriage_Left.stl
|  |  |  |
| 1 x Y_Carriage_Right.stl |
|----------|
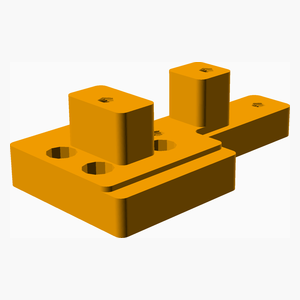
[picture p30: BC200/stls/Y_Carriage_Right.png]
Y_Carriage_Right.stl
|  |

### Sub-assemblies

| 1 x Top_Face_Stage_1_assembly |
|----------|
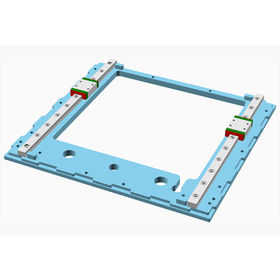
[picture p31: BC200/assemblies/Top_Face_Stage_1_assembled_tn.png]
Top_Face_Stage_1_assembled
|  |

### Assembly instructions

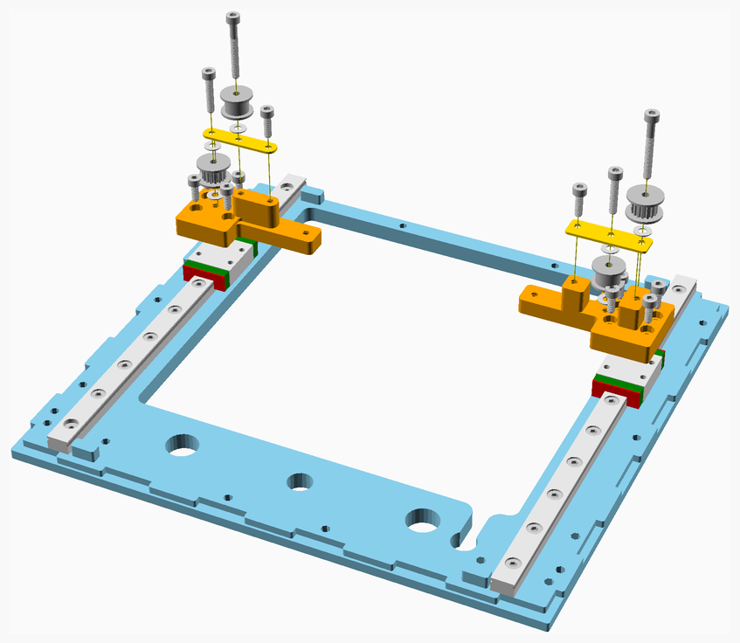
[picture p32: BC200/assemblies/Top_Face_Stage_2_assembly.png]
Top_Face_Stage_2_assembly


Attach the left and right **Y_carriages** to the top face rails. Note that the two carriages are not interchangeable
so be sure to attach them as shown in the diagram.

The carriages should be attached to the rails before the pulleys are added, since otherwise the bolts are not
accessible.  
Attach the pulleys to the carriages. Note that the toothless pulleys are on the inside. Note also that there is a
washer under each of the upper pulleys, but not on top of those pulleys.

Tighten the pulley bolts until the pulleys stop running freely, and then loosen them slightly (approximately 1/16
of a turn) so they run freely.

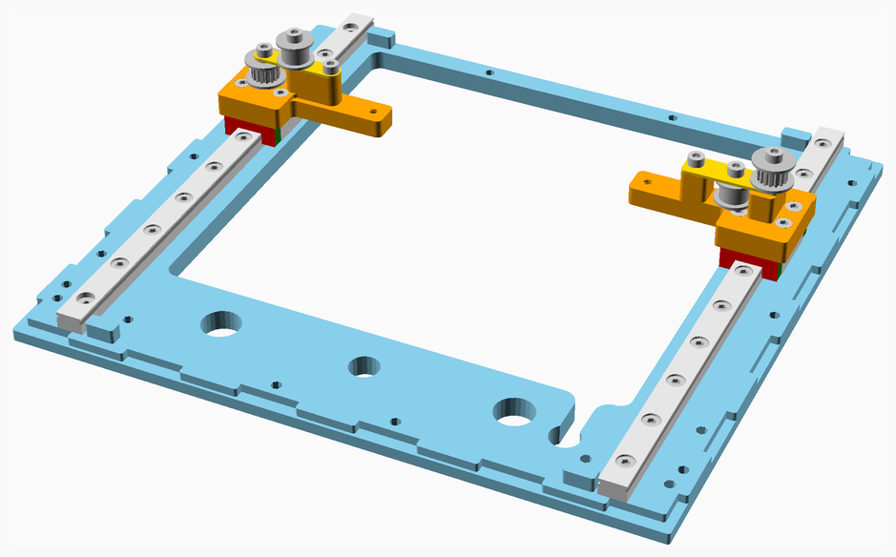
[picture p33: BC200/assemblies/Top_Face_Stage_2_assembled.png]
Top_Face_Stage_2_assembled


<span></span>
[Top](#TOP)

---

## Top_Face assembly

### Vitamins

| Qty | Description |
|----:|:---|
| 4 | Bolt M3 caphead x 10mm |
| 1 | Linear rail MGN9 x 150mm |
| 1 | Linear rail carriage MGN9C |

### Sub-assemblies

| 1 x Top_Face_Stage_2_assembly |
|----------|
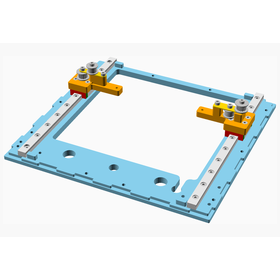
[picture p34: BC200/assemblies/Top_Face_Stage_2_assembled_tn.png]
Top_Face_Stage_2_assembled
|  |

### Assembly instructions

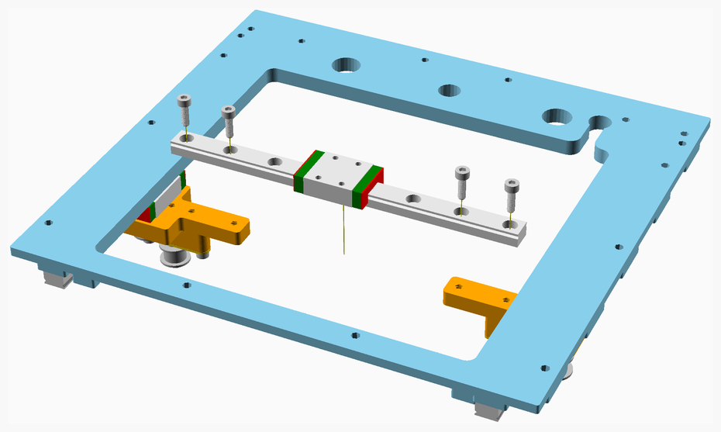
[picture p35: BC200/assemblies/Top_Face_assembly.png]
Top_Face_assembly


1. Turn the **Top_Face** into its normal orientation.
2. Bolt the X-axis linear rail onto the Y carriages.
3. Turn the Top_Face upside down again and place it on a flat surface.
4. Align the left and right Y-axis linear rails. Do this by pushing the X-axis rail to the rear of the **Top_Face** and tighten
the corresponding bolts (left loose in a previous step) and then push the X-axis rails to the front of the **Top_Face**,
again tightening the corresponding bolts.
5. Check that the carriages run smoothly on the Y-axis linear rails.

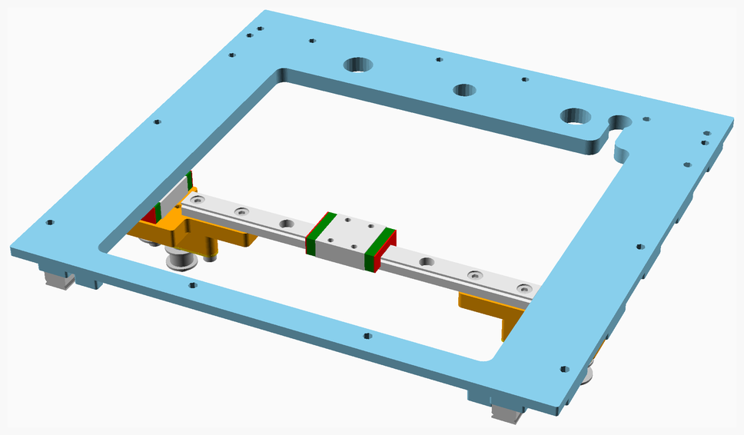
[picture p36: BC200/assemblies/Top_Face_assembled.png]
Top_Face_assembled


<span></span>
[Top](#TOP)

---

## Display_Cover assembly

### Vitamins

| Qty | Description |
|----:|:---|
| 1 | BigTreeTech TFT35 v3.0 |
| 4 | Bolt M3 caphead x  6mm |

### 3D Printed parts

| 1 x Display_Housing.stl |
|----------|
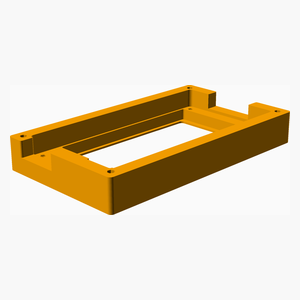
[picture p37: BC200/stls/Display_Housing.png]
Display_Housing.stl
|  |

### Assembly instructions

Display_Cover_assembly

Place the display into the housing and secure it with the bolts - use the bolts to self-tap the holes in the housing.
Attach the knob to the display.

Display_Cover_assembled

<span></span>
[Top](#TOP)

---

## Display_Housing assembly

### Vitamins

| Qty | Description |
|----:|:---|
| 4 | Bolt M3 buttonhead x 16mm |
| 4 | Bolt M3 caphead x 16mm |

### 3D Printed parts

| 1 x Display_Housing_Bracket.stl | 1 x Front_Lower_Chord.stl |
|---|---|
| Display_Housing_Bracket.stl | Front_Lower_Chord.stl |

### Sub-assemblies

| 1 x Display_Cover_assembly |
|----------|
| Display_Cover_assembled |

### Assembly instructions

Display_Housing_assembly

1. Bolt the **Display_Cover_assembly** to the **Display_Housing_Bracket**.
2. Bolt the **Display_Housing_Bracket** to **the Front_Lower_Chord**.

Display_Housing_assembled

<span></span>
[Top](#TOP)

---

## Z_Carriage assembly

### Vitamins

| Qty | Description |
|----:|:---|
| 4 | Bolt M3 caphead x  8mm |
| 1 | Leadscrew nut 8 x 2 |
| 2 | Linear bearing LM12LUU |

### 3D Printed parts

| 1 x Z_Carriage.stl |
|----------|
| Z_Carriage.stl |

### Assembly instructions

Z_Carriage_assembly

Slide the linear bearings into the Z_Carriage.

Affix the leadscrew nut.

Z_Carriage_assembled

<span></span>
[Top](#TOP)

---

## Print_bed assembly

### Vitamins

| Qty | Description |
|----:|:---|
| 4 | Bolt M3 caphead x 16mm |
| 1 | Cork underlay 105mm x 105mm x 3mm |
| 1 | Magnetic base 100mm x 100mm |
| 8 | O-ring nitrile 4mm x 2mm |
| 1 | OpenBuilds mini heated bed 100mm x 100mm |
| 1 | Print surface 100mm x 100mm |
| 8 | Washer M3 |
| 2 | Ziptie 2.5mm x 100mm min length |

### Sub-assemblies

| 1 x Z_Carriage_assembly |
|----------|
| Z_Carriage_assembled |

### Assembly instructions

Print_bed_assembly

This is the standard variant of the print bed, using an OpenBuilds 100mm heated bed. There is also a version using
a 120 x 120 x 6 mm aluminium tooling plate, see [printbed 120](../../PRINTBED120/readme.md).

1. Prepare the the cork underlay by cutting it to size, making a cutout for the heated bed wiring, and making cutouts
for the bolts and O-rings.
2. Prepare the magnetic base by drilling holes for the bolts.
3. Prepare the heated bed by soldering on the wires and sticking on the magnetic base. Drill bolt holes in the magnetic base.
4. Place the cork underlay on the **Z_Carriage** and place the heated bed on top.
5. Secure the heated bed to the **Z_Carriage**, using the bolts and O-rings. The O-rings allow for bed leveling and help
thermally insulate the heated bed from the **Z_Carriage**.
6. Secure the heated bed wiring to the underside of the printbed using zipties.

Print_bed_assembled

<span></span>
[Top](#TOP)

---

## Back_Face_Stage_1 assembly

### Vitamins

| Qty | Description |
|----:|:---|
| 8 | Bolt M5 countersunk x 16mm |
| 8 | Nut M5 nyloc |
| 4 | SK12 shaft support bracket |

### 3D Printed parts

| 1 x Back_Face.stl |
|----------|
| Back_Face.stl |

### Assembly instructions

Back_Face_Stage_1_assembly

Attach the SK brackets to the **Back_Face**. Note the orientation of the tightening bolts: the top tightening bolts should
face inward and the bottom tightening bolts should face outward. This allows access after the BabyCube is fully assembled.

Back_Face_Stage_1_assembled

<span></span>
[Top](#TOP)

---

## Back_Face assembly

### Vitamins

| Qty | Description |
|----:|:---|
| 4 | Bolt M3 buttonhead x 12mm |
| 1 | Cork damper NEMA 17 |
| 1 | Leadscrew 8mm x 150mm |
| 2 | Linear rod 12mm x 200mm |
| 1 | Stepper motor NEMA17 x 34mm |
| 1 | Stepper motor cable, 150mm |

### Sub-assemblies

| 1 x Back_Face_Stage_1_assembly | 1 x Print_bed_assembly |
|---|---|
| Back_Face_Stage_1_assembled | Print_bed_assembled |

### Assembly instructions

Back_Face_assembly

1. Slide the linear rods through the SK brackets and the printbed bearings.
2. Tighten the bolts in the SK brackets, ensuring the **Z_Carriage** slides freely on the rods.
3. Place the cork damper on the stepper motor and thread the lead screw through the leadnut and attach the stepper motor
  to the **Back_Face**. Note the orientation of the JST socket.

Back_Face_assembled

<span></span>
[Top](#TOP)

---

## Right_Face_Stage_1 assembly

### Vitamins

| Qty | Description |
|----:|:---|
| 4 | Bolt M3 buttonhead x 12mm |
| 1 | Bolt M3 countersunk x 35mm |
| 1 | Cork damper NEMA 14 |
| 2 | Pulley GT2 idler 16 teeth |
| 1 | Pulley GT2UM 20 teeth |
| 1 | Stepper motor NEMA14 x 36mm |
| 1 | Stepper motor cable, 400mm |
| 6 | Washer M3 |
| 3 | Ziptie 2.5mm x 100mm min length |

### 3D Printed parts

| 1 x Right_Face.stl |
|----------|
| Right_Face.stl |

### Assembly instructions

Right_Face_Stage_1_assembly

1. Place the cork damper on the stepper motor and bolt the motor to the frame.
Note the cork damper is important as it provides thermal insulation between the stepper motor and the frame.
Note orientation of the JST connector.
2. Attach the toothed idler pulleys to the frame, separated by the washers as shown.
3. Thread the zip ties through the frame, but do not tighten them yet, since the extruder motor cable will also go through
the zip ties.

Right_Face_Stage_1_assembled

<span></span>
[Top](#TOP)

---

## Right_Face assembly

### Vitamins

| Qty | Description |
|----:|:---|
| 1 | Cork damper NEMA 17 |
| 1 | MK10 Dual Pulley Extruder |
| 1 | Stepper motor NEMA17 x 40mm |
| 1 | Stepper motor cable, 400mm |
| 2 | Ziptie 2.5mm x 100mm min length |

### Sub-assemblies

| 1 x Right_Face_Stage_1_assembly |
|----------|
| Right_Face_Stage_1_assembled |

### Assembly instructions

Right_Face_assembly

1. Attach the extruder gear to the stepper motor.
2. Place the cork damper on the stepper motor and attach the motor through the frame to the extruder. Note the cork
damper is important as it provides thermal insulation between the stepper motor and the frame.
3. Secure the cables for both motors with the zip ties.

Right_Face_assembled

<span></span>
[Top](#TOP)

---

## Base assembly

### Vitamins

| Qty | Description |
|----:|:---|
| 1 | Aluminium box section 12mm x 8mm x 1mm, length 85mm |
| 1 | Aluminium sheet 220mm x 204mm x 3mm |
| 1 | BigTreeTech SKR Mini E3 v2.0 |
| 2 | Bolt M3 buttonhead x 10mm |
| 4 | Bolt M3 caphead x  6mm |
|  14 | Bolt M3 caphead x  8mm |
| 1 | Micro SD card |
| 9 | Pillar hex nylon F/F M3x12 |
| 1 | Raspberry Pi 3A+ |

### 3D Printed parts

| 1 x Base.stl | 1 x Base_Template.stl | 1 x PSU_Bracket.stl |
|---|---|---|
| Base.stl | Base_Template.stl | PSU_Bracket.stl |
| 2 x PSU_Support.stl |
|----------|
| PSU_Support.stl |

### CNC Routed parts

| 1 x BaseAL.dxf |
|----------|
| BaseAL.dxf |

### Assembly instructions

Base_assembly

1. Attach the Base_Template to the aluminium sheet and use it to drill out the holes. The base template has 2mm holes
marked out for pilot holes. Once you have drilled these re-drill the holes with a 3mm bit. Note that the Base_Template
has holes marked for the BTT E3 Mini V2, the BTT E3 Turbo and the BTT STL 1.4 boards - choose the appropriate holes for
your board. If you are unable to source an aluminium sheet, it is possible to print and use the Base.stl file, but
using and aluminium plate is much preferred.
2. Attach the PSU_Supports to the base plate with double sided tape.
3. Bolt the PSU_Bracket to the base plate.
4. Attach the PSU to the base plate with the velcro straps.
5. Cover the top and bottom sides of the box section with thermal paste.
6. Attach the box section to the bottom of the control board with electrical tape. The tape serves to keep the box
section in place until it is attached to the base plate.
7. Using the hex pillars, attach the control board to the base plate.

Base_assembled

<span></span>
[Top](#TOP)

---

## Switch_Shroud assembly

### Vitamins

| Qty | Description |
|----:|:---|
| 1 | Bolt M3 buttonhead x 10mm |
| 2 | Wire black 12SWG, length 100mm |
| 2 | Wire red 12SWG, length 100mm |
| 1 | XT60 Connector Female |
| 1 | XT60 Connector Female - not shown |
| 1 | XT60 Connector Male |
| 1 | XT60 Connector Male - not shown |

### 3D Printed parts

| 1 x Switch_Shroud.stl | 1 x Switch_Shroud_Clamp.stl |
|---|---|
| Switch_Shroud.stl | Switch_Shroud_Clamp.stl |

### Assembly instructions

Switch_Shroud_assembly

Place the XT60 connectors through the Switch_Shroud and bolt on the Switch_Shroud_Clamp to keep them in place.

Switch_Shroud_assembled

<span></span>
[Top](#TOP)

---

## Left_Face assembly

### Vitamins

| Qty | Description |
|----:|:---|
| 4 | Bolt M3 buttonhead x 12mm |
| 2 | Bolt M3 countersunk x 12mm |
| 2 | Bolt M3 countersunk x 16mm |
| 1 | Bolt M3 countersunk x 35mm |
| 1 | Cork damper NEMA 14 |
| 2 | Pulley GT2 idler 16 teeth |
| 1 | Pulley GT2UM 20 teeth |
| 1 | Rocker Switch PRASA1-16F-BB0BW |
| 1 | Stepper motor NEMA14 x 36mm |
| 1 | Stepper motor cable, 400mm |
| 6 | Washer M3 |
| 4 | Ziptie 2.5mm x 100mm min length |

### 3D Printed parts

| 1 x Left_Face.stl |
|----------|
| Left_Face.stl |

### Sub-assemblies

| 1 x Switch_Shroud_assembly |
|----------|
| Switch_Shroud_assembled |

### Assembly instructions

Left_Face_assembly

1. Place the cork damper on the stepper motor and bolt the motor to the frame.
Note the cork damper is important as it provides thermal insulation between the stepper motor and the frame.
Note orientation of the JST connector.
2. Secure the motor wires with zip ties.
3. Bolt the two front idler pulleys with washers to the frame.
4. Attach the wires to the switch and bolt the **Switch_Shroud** to the left face.

Left_Face_assembled

<span></span>
[Top](#TOP)

---

## Stage_1 assembly

### Vitamins

| Qty | Description |
|----:|:---|
| 2 | Bolt M3 buttonhead x  8mm |
| 8 | Bolt M3 buttonhead x 12mm |

### 3D Printed parts

| 4 x Foot_LShaped_8mm.stl |
|----------|
| Foot_LShaped_8mm.stl |

### Sub-assemblies

| 1 x Base_assembly | 1 x Left_Face_assembly | 1 x Right_Face_assembly |
|---|---|---|
| Base_assembled | Left_Face_assembled | Right_Face_assembled |

### Assembly instructions

Stage_1_assembly

1. Bolt the Left_Face and the left feet to the base.
2. Bolt the Right_Face and the right feet to the base.

Stage_1_assembled

<span></span>
[Top](#TOP)

---

## Stage_2 assembly

### Vitamins

| Qty | Description |
|----:|:---|
| 2 | Bolt M3 buttonhead x 10mm |
| 6 | Bolt M3 countersunk x  6mm |
| 4 | Bolt M3 countersunk x 10mm |
| 4 | Ziptie 2.5mm x 100mm min length |

### Sub-assemblies

| 1 x Back_Face_assembly | 1 x Stage_1_assembly |
|---|---|
| Back_Face_assembled | Stage_1_assembled |

### Assembly instructions

Stage_2_assembly

Add the Back_Face and bolt it to the left and right faces and the base.

Stage_2_assembled

<span></span>
[Top](#TOP)

---

## Stage_3 assembly

### Vitamins

| Qty | Description |
|----:|:---|
| 2 | Bolt M3 buttonhead x 10mm |
| 8 | Bolt M3 countersunk x 10mm |

### 3D Printed parts

| 1 x Front_Upper_Chord.stl |
|----------|
| Front_Upper_Chord.stl |

### Sub-assemblies

| 1 x Display_Housing_assembly | 1 x Stage_2_assembly |
|---|---|
| Display_Housing_assembled | Stage_2_assembled |

### Assembly instructions

Stage_3_assembly

Bolt the BabyCube nameplate and the Display_Housing to the front of the frame.

Stage_3_assembled

<span></span>
[Top](#TOP)

---

## Stage_4 assembly

### Vitamins

| Qty | Description |
|----:|:---|
|  10 | Bolt M3 buttonhead x 12mm |

### Sub-assemblies

| 1 x Stage_3_assembly | 1 x Top_Face_assembly |
|---|---|
| Stage_3_assembled | Top_Face_assembled |

### Assembly instructions

Stage_4_assembly

Add the Top_Face.

Stage_4_assembled

<span></span>
[Top](#TOP)

---

## Stage_5 assembly

### Vitamins

| Qty | Description |
|----:|:---|
| 1 | Belt GT2 x 6mm x 728mm |
| 1 | Belt GT2 x 6mm x 728mm |
| 2 | Bolt M3 countersunk x 10mm |
| 2 | Bolt M3 countersunk x 12mm |

### 3D Printed parts

| 1 x X_Carriage_Belt_Clamp.stl |
|----------|
| X_Carriage_Belt_Clamp.stl |

### Sub-assemblies

| 1 x Stage_4_assembly | 1 x X_Carriage_Belt_Side_MGN9C_assembly |
|---|---|
| Stage_4_assembled | X_Carriage_Belt_Side_MGN9C_assembled |

### Assembly instructions

Stage_5_assembly

1. Add the Printhead.
2. Thread the belts in the pattern shown.
3. Adjust the belts tension.

Stage_5_assembled

<span></span>
[Top](#TOP)

---

## main assembly

### Vitamins

| Qty | Description |
|----:|:---|
| 2 | Bolt M3 countersunk x 12mm |
| 4 | Bolt M3 countersunk x 30mm |
| 1 | PTFE tube 292 mm |
| 1 | Spiral wrap, 500mm |

### 3D Printed parts

| 1 x Spool_Holder.stl |
|----------|
| Spool_Holder.stl |

### Sub-assemblies

| 1 x Printhead_E3DV6_MGN9C_assembly | 1 x Stage_5_assembly |
|---|---|
| Printhead_E3DV6_MGN9C_assembled | Stage_5_assembled |

### Assembly instructions

main_assembly

1. Connect the wiring to the print head.
2. Connect the Bowden tube.
3. Add the spool holder.
4. Calibrate the printer.

main_assembled

<span></span>
[Top](#TOP)

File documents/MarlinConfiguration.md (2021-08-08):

# Marlin Configuration

D - Disable, ie place `//` at the start of a line<br>
E - Enable, ie delete the `//` at the start of a line<br>
C - Change<br>
E&C - Enable and Change

## Configuration.h

```h
C
#define SERIAL_PORT 2
E
#define SERIAL_PORT_2 -1
E&C
#define CUSTOM_MACHINE_NAME "BabyCube"
E
#define PIDTEMPBED
E
#define COREXY
D
//#define USE_ZMIN_PLUG
E
#define USE_ZMAX_PLUG
C
#define X_DRIVER_TYPE  TMC2209
#define Y_DRIVER_TYPE  TMC2209
#define Z_DRIVER_TYPE  TMC2209
#define E0_DRIVER_TYPE TMC2209
C
#define DEFAULT_AXIS_STEPS_PER_UNIT   { 80, 80, 400, 136 }
D
//#define Z_MIN_PROBE_USES_Z_MIN_ENDSTOP_PIN
E
#define PROBE_MANUALLY
C
#define INVERT_Y_DIR false
#define INVERT_Z_DIR true
#define INVERT_E0_DIR true
C
#define Z_HOME_DIR 1
C
#define X_BED_SIZE 100
#define Y_BED_SIZE 75

C
#define X_MIN_POS -12
#define Y_MIN_POS 0
#define Z_MAX_POS 60
E
#define AUTO_BED_LEVELING_3POINT
E
#define RESTORE_LEVELING_AFTER_G28
C
#define HOMING_FEEDRATE_MM_M { (20*60), (20*60), (2*60) }
E
#define EEPROM_SETTINGS
E
#define SDSUPPORT
E
#define SD_CHECK_AND_RETRY
E
#define INDIVIDUAL_AXIS_HOMING_MENU
E
#define SPEAKER
E
#define CR10_STOCKDISPLAY
```

## Configuration_adv.h

```h
C
#define PID_EXTRUSION_SCALING
C
#define THERMAL_PROTECTION_PERIOD 60        // Seconds
C
#define THERMAL_PROTECTION_HYSTERESIS 10     // Degrees Celsius
C
#define WATCH_TEMP_PERIOD  30               // Seconds
C
#define THERMAL_PROTECTION_BED_PERIOD        60 // Seconds
C
#define THERMAL_PROTECTION_BED_HYSTERESIS     10 // Degrees Celsius
C
#define FAN_MAX_PWM 157  // To run 12V fan at 19.5V, 12/19.5*255=157
C
#define E0_AUTO_FAN_PIN FAN1_PIN
C
#define EXTRUDER_AUTO_FAN_SPEED 150  // To run 12V fan at 19.5V, 12/19.5*255=157, set to 150, just below max speed to reduce noise
E
#define SENSORLESS_BACKOFF_MM  { 2, 2, 0 }       // (mm) Backoff from endstops before sensorless homing
C
#define HOMING_BUMP_MM      { 0, 0, 0 }       // (mm) Backoff from endstops after first bump
C
#define HOMING_BACKOFF_POST_MM { 2, 2, 2 }    // (mm) Backoff from endstops after homing
E
#define HOME_Y_BEFORE_X                       // If G28 contains XY home Y before X
E
#define STATUS_MESSAGE_SCROLLING
E
#define LCD_SET_PROGRESS_MANUALLY
C
#define EVENT_GCODE_SD_ABORT "G28XY\nM84" // G-code to run on SD Abort Print (e.g., "G28XY" or "G27")
E
#define LONG_FILENAME_HOST_SUPPORT
E
#define SCROLL_LONG_FILENAMES
E
#define BABYSTEPPING
E
#define BABYSTEP_WITHOUT_HOMING
E
#define BABYSTEP_ZPROBE_OFFSET            // Combine M851 Z and Babystepping
E
#define LIN_ADVANCE
C
#define LIN_ADVANCE_K 0.0     // Unit: mm compression per 1mm/s extruder speed
C
#define X_CURRENT       600        // (mA) RMS current. Multiply by 1.414 for peak current.
C
#define Y_CURRENT       600
D
//#define STEALTHCHOP_Z
D
//#define STEALTHCHOP_E
C
#define CHOPPER_TIMING CHOPPER_DEFAULT_19V        // All axes (override below)
E
#define HYBRID_THRESHOLD
E
#define SENSORLESS_HOMING // StallGuard capable drivers only
C
#define X_STALL_SENSITIVITY  45
C
#define Y_STALL_SENSITIVITY  15
C
#define Z_STALL_SENSITIVITY  100
E
#define IMPROVE_HOMING_RELIABILITY
E
#define HOST_ACTION_COMMANDS
```

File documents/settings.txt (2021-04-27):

M503
  G21    ; Units in mm (mm)

  M149 C ; Units in Celsius

;(c Steps per unit:
  M92 X80.00 Y80.00 Z3200.00 E135.00

;(c not explicit) Material heatup parameters:
  M145 S0 H185 B45 F255
  M145 S1 H240 B110 F255

; Filament settings: Disabled
  M200 S0 D1.75
;(c) Maximum feedrates (units/s):
  M203 X500.00 Y500.00 Z10.00 E25.00
;(c) Maximum Acceleration (units/s2):
  M201 X500.00 Y500.00 Z100.00 E5000.00
;(c) Acceleration (units/s2): P<print_accel> R T
  M204 P500.00 R500.00 T500.00
;(c) Advanced: B S T J
  M205 B20000.00 S0.00 T0.00 J0.08
;(x but see Z_MAX_POS in c) Home offset:
  M206 X0.00 Y0.00 Z-4.90

;(c not explicit) PID settings:
  M301 P33.27 I2.56 D108.03

;(ca not explicit) Driver stepping mode:
  M569 S1 X Y

;(ca not explicit) Filament load/unload lengths:
  M603 L350.00 U400.00

;(c not explicit)  Z-Probe Offset (mm):
  M851 X10.00 Y10.00 Z0.00

;(ca not explicit) Linear Advance:
  M900 K0.00

;(ca not explicit) Stepper driver current:
  M906 X800 Y800 Z1000
  M906 T0 E800

;(ca not explicit) StallGuard threshold:
  M914 X45 Y15 Z100

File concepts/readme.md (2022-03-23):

# BabyCube Carbon Fiber

The carbon fiber version of the BabyCube is very much a work in progress. Here's an illustration demonstrating proof of concept:

BabyCubeCF

The exploded version:

BabyCubeCF exploded

## License

BabyCube is licensed under the [Creative Commons Attribution-NonCommercial-ShareAlike 4.0 International License](https://creativecommons.org/licenses/by-nc-sa/4.0/)
(CC BY-NC-SA 4.0)<br />
<a rel="license" href="http://creativecommons.org/licenses/by-nc-sa/4.0/">
</a>

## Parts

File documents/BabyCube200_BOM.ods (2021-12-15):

Total Cost |  |  | 250.01
Item | Quantity | Price | Cost
Motion system XY
Stepper motor NEMA14 x 36mm | 2 | 12.46 | 24.92
Stepper motor cable, length 400mm | 2 |  | 0.00 | included with stepper motor
Linear rail MGN9 x 150mm | 1 | 5.70 | 5.70
Linear rail MGN9 x 200mm | 2 | 6.67 | 13.34
Pulley GT2 idler smooth 9.63mm | 2 | 0.60 | 1.20
Pulley GT2 idler 16 teeth | 6 | 0.60 | 3.60
Pulley GT2UM 20 teeth | 2 | 0.75 | 1.50
Belt GT2 x 6mm x 2m | 1 | 4.46 | 4.46
Motion system Z
Stepper motor NEMA17 x 34mm with integrated 150mm lead screw | 1 | 18.25 | 18.25
Stepper motor cable, length 150mm | 1 |  | 0.00 | included with stepper motor
Linear rod 12mm x 200mm | 2 | 3.05 | 6.10
Linear bearing LM12LUU | 2 | 1.90 | 3.80
SK12 shaft support bracket | 4 | 1.75 | 7.00
Nut M5nyloc | 8 | 0.24 | 1.92
Extruder
MK10 Dual Pulley Extruder | 1 | 6.56 | 6.56
Stepper motor NEMA17 x 40mm | 1 | 9.80 | 9.80
Hot end
E3D v6 Hotend Full Kit | 0 | 52.80 | 0.00 | includes everything for hotend except radial fan
Hot end E3D V6 direct 1.75mm | 1
30W Cartridge heater | 1
Thermistor sensor cartridge | 1
Fan 30mm x 10mm | 1
E3D V6 Fan Duct | 1
Hot end fixings kit | 2
PTFE tube 238 mm | 1
Silicone sock | 1
Square radial fan 3010 | 0 | 5.99 | 0.00
Haldis 3D hotend kit | 1 | 22.00 | 22.00
Printbed
OpenBuilds mini heated bed 100mm x 100mm | 1 | 11.50 | 11.50
Cork underlay 105mm x 105mm x 3mm | 1 | 2.99 | 2.99
Print surface 100mm x 100mm | 1 | 9.27 | 9.27 | cut from Ender3 print surface
Magnetic base 100mm x 100mm | 1 |  | 0.00 | included with print surface
O-ring nitrile 3mm x 2mm | 4 | 0.25 | 1.00
Electronics and related
BigTreeTech SKR Mini E3 v2.0 | 1 | 30.37 | 30.37
Pillar hex nylon F/F M3x12 | 5 | 0.01 | 0.05
Aluminium rectangular box section 12mm x 8mm x 1mm, length 85mm | 1 | 1.39 | 1.39
BigTreeTech TFT35 v3.0 | 1 | 27.18 | 27.18
FSKE 120W 19V 6.32A Laptop Charger for ASUS | 1 | 22.99 | 22.99
Rocker Switch PRASA1-16F-BB0BW | 1 | 1.84 | 1.84
XT60 Connector Female | 2 | 0.17 | 0.34
XT60 Connector Male | 2 | 0.17 | 0.34
Wire black 12SWG, length 100mm | 2 |  | 0.00 | use wire from DC side of PSU
Wire red 12SWG, length 100mm | 2 |  | 0.00
Aluminium plate 220mm x 204mm x 3mm | 1 | 4.99 | 4.99
Nuts and Bolts
Bolt M2 caphead x 6mm | 4 | 0.01 | 0.04
Bolt M3 caphead x 10mm | 12 | 0.01 | 0.12
Bolt M3 caphead x 16mm | 6 | 0.01 | 0.06
Bolt M3 caphead x 20mm | 2 | 0.01 | 0.02
Bolt M3 caphead x 25mm | 2 | 0.01 | 0.02
Bolt M3 caphead x 6mm | 9 | 0.01 | 0.09
Bolt M3 caphead x 8mm | 27 | 0.01 | 0.27
Bolt M3 countersunk x 10mm | 14 | 0.01 | 0.14
Bolt M3 countersunk x 12mm | 2 | 0.01 | 0.02
Bolt M3 countersunk x 16mm | 6 | 0.01 | 0.06
Bolt M3 countersunk x 30mm | 2 | 0.01 | 0.02
Bolt M3 countersunk x 6mm | 6 | 0.01 | 0.06
Bolt M3 buttonhead x 10mm | 21 | 0.01 | 0.21
Bolt M3 buttonhead x 12mm | 26 | 0.01 | 0.26
Bolt M3 buttonhead x 16mm | 4 | 0.01 | 0.04
Bolt M3 buttonhead x 25mm | 2 | 0.01 | 0.02
Bolt M3 buttonhead x 8mm | 10 | 0.01 | 0.10
Bolt M5 countersunk x 16mm | 8 | 0.10 | 0.80
Washer M3 | 12 | 0.01 | 0.12
Cable Management
Ziptie 2.5mm x 100mm min length | 17 |  | 0.99 | pack of 100
Spiral wrap, 500mm | 1 | 2.15 | 2.15
Tools
M3 tap set | 1 | 7.85
1080 assorted M2 M3 M4 nuts, bolts and washers set |  | 9.85
Voron V0 3d printer aluminum anodized plate and 120x120mm Double Side Textured/Smooth PEI Spring steel sheet |  | 31.94
Silicone heating pad heater 100mmx100mm for 3d printer heat bed |  | 4.74

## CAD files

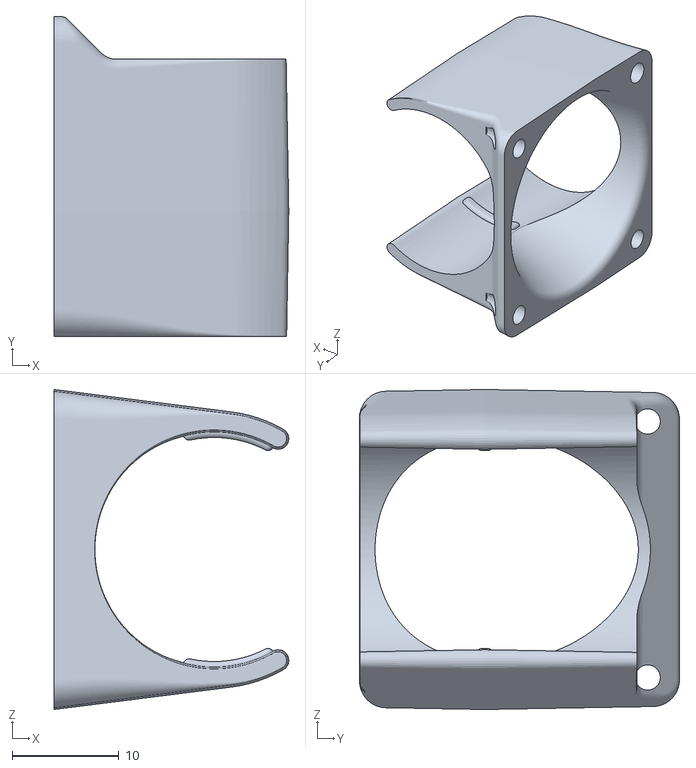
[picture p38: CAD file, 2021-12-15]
scad/stlimport/E3D_V6_6_Duct.stl
22.0 x 30.0 x 30.0

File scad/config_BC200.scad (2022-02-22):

_variant = "BC200";

_useCNC = false;

_backPlateOutset = [0, 4];

_tabTolerance = 0.0; // for 3D printed parts

_chordLengths = [220, 200, 200];

eSizeX = 8;

_xyMotorDescriptor = "NEMA14";
_zMotorDescriptor = "NEMA17_34L150";

_psuDescriptor = "ASUS_FSKE_120W";

// set _fullLengthYRail to add end cutouts for Y rail
_fullLengthYRail = true;
_xRailLength = 150;
_yRailLength = 200;
_xCarriageDescriptor = "MGN9C";
_xCarriageCountersunk = true;
_yCarriageDescriptor = "MGN9C";
_coreXYDescriptor = "GT2_20_16";

_useFrontDisplay = true;
_useFrontSwitch = true;

_printBedSize = 100;

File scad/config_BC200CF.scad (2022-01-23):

_variant = "BC200CF";

_useCNC = true;

_backPlateOutset = [0, 0];

_tabTolerance = 0.05; // for CNC, 0.05 each side gives 0.1 total tolerance

_chordLengths = [220, 200, 200];

eSizeX = 10;

_xyMotorDescriptor = "NEMA14";
_zMotorDescriptor = "NEMA17_34L150";

_psuDescriptor = "NG_CB_200W_24V";

// set _fullLengthYRail to add end cutouts for Y rail
_fullLengthYRail = true;
_xRailLength = 150;
_yRailLength = 200;
_xCarriageDescriptor = "MGN9C";
_xCarriageCountersunk = true;
_yCarriageDescriptor = "MGN9C";
_coreXYDescriptor = "GT2_20_16";

_useFrontDisplay = false;
_useFrontSwitch = false;

_printBedSize = 120;

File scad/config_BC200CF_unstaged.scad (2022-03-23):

include <config_BC200CF.scad>
_variant = "BC200CF_debug";

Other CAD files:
scad/config_BC200NEMA17.scad
scad/Main.scad
scad/MainAssembly.scad
scad/MainAssemblyCF.scad
scad/MainCF.scad
scad/MainPRINTBED120.scad
scad/MainPRINTBED120E15.scad
scad/Parameters_CoreXY.scad
scad/Parameters_Main.scad
scad/Parameters_Positions.scad
scad/config_BC200_test.scad
scad/config_BC220.scad
scad/config_BC250.scad
scad/config_PRINTBED120E15.scad
scad/global_defs.scad
scad/printed/BackFace.scad
scad/printed/BackFaceAssemblies.scad
scad/printed/Base.scad
scad/printed/DisplayHousing.scad
scad/printed/DisplayHousingAssemblies.scad
scad/printed/Extras.scad
scad/printed/Foot.scad
scad/printed/FrontChords.scad
scad/printed/FrontFace.scad
scad/printed/LeftAndRightFaceAssemblies.scad
scad/printed/LeftAndRightFaceAssembliesCF.scad
scad/printed/LeftAndRightFaces.scad
scad/printed/Printbed.scad
scad/printed/Printbed3point.scad
scad/printed/Printhead.scad
scad/printed/PrintheadAssemblies.scad
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

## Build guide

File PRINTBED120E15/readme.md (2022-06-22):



# Print Bed 3 Point Printed Assembly Instructions

This is a alternative print bed for the BabyCube. It uses the same 120 x 120 x 6 mm aluminium tooling plate that is used on the
[Voron0](https://vorondesign.com/voron0).

Print Bed 3 Point Printed Assembly

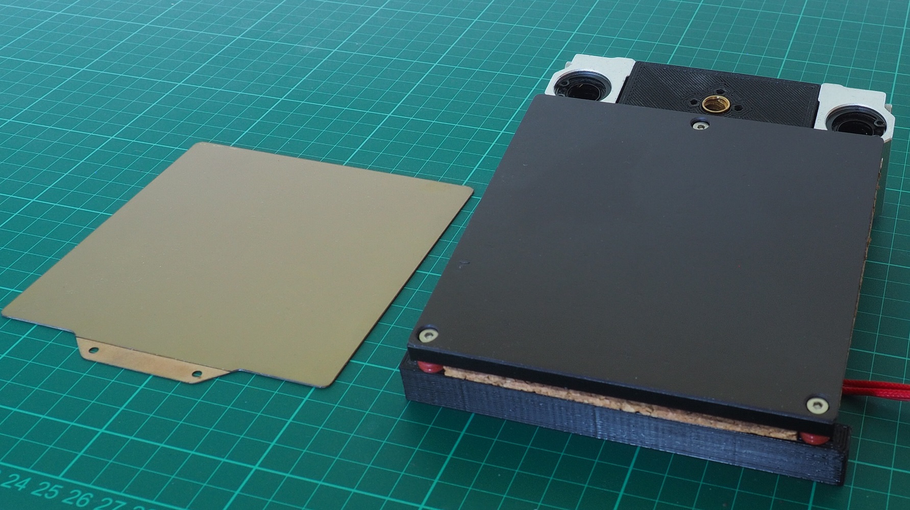
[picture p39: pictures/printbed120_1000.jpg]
printbed120


<span></span>

---

## Table of Contents

1. [Parts list](#Parts_list)
1. [Print_bed_3_point assembly](#Print_bed_3_point_assembly)

<span></span>
[Top](#TOP)

---

## Parts list

| <span style="writing-mode: vertical-rl; text-orientation: mixed;">Print Bed 3 Point</span> | <span style="writing-mode: vertical-rl; text-orientation: mixed;">TOTALS</span> |  |
|-----:|---:|:---|
| | | **Vitamins** |
| 1  | 1  |  Aluminium tooling plate 120mm x 120mm x 6mm |
| 4  | 4  |  Bolt M3 caphead x  8mm |
| 4  | 4  |  Bolt M3 caphead x 35mm |
| 2  | 2  |  Bolt M4 buttonhead x 12mm |
| 4  | 4  |  Bolt M5 countersunk x 12mm |
| 1  | 1  |  Cork underlay 120mm x 120mm x 3mm |
| 1  | 1  |  Extrusion E1515 x 130mm |
| 2  | 2  |  Extrusion E1515 x 150mm |
| 1  | 1  |  Heating pad 100mm x 100mm |
| 1  | 1  |  Leadscrew nut 8 x 2 |
| 1  | 1  |  Magnetic base 120mm x 120mm |
| 2  | 2  |  SCS12UU bearing block |
| 2  | 2  |  Washer M4 |
|  26  | 26  | Total vitamins count |

<span></span>
[Top](#TOP)

---

## Print_bed_3_point assembly

### Vitamins

| Qty | Description |
|----:|:---|
| 1 | Aluminium tooling plate 120mm x 120mm x 6mm |
| 4 | Bolt M3 caphead x  8mm |
| 4 | Bolt M3 caphead x 35mm |
| 2 | Bolt M4 buttonhead x 12mm |
| 4 | Bolt M5 countersunk x 12mm |
| 1 | Cork underlay 120mm x 120mm x 3mm |
| 1 | Extrusion E1515 x 130mm |
| 2 | Extrusion E1515 x 150mm |
| 1 | Heating pad 100mm x 100mm |
| 1 | Leadscrew nut 8 x 2 |
| 1 | Magnetic base 120mm x 120mm |
| 2 | SCS12UU bearing block |
| 2 | Washer M4 |

### Assembly instructions

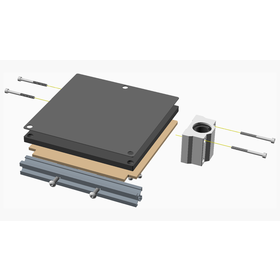
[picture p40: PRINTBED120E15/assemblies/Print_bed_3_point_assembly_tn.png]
Print_bed_3_point_assembly


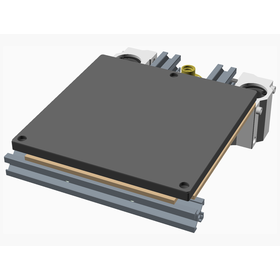
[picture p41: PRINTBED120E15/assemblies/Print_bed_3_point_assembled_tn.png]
Print_bed_3_point_assembled


<span></span>
[Top](#TOP)

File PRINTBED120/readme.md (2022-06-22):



# Print Bed 3 Point Printed Assembly Instructions

This is a alternative print bed for the BabyCube. It uses the same 120 x 120 x 6 mm aluminium tooling plate that is used on the
[Voron0](https://vorondesign.com/voron0).

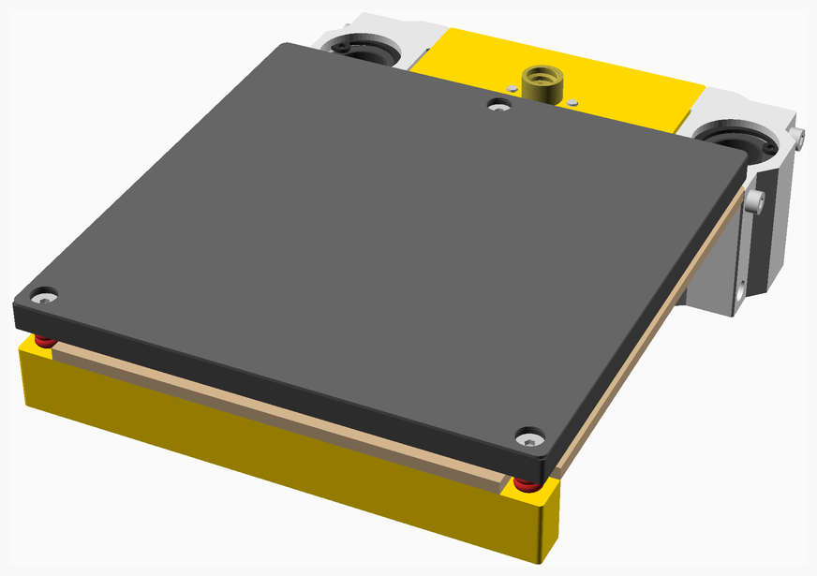
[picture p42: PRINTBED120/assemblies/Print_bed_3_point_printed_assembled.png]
Print Bed 3 Point Printed Assembly


printbed120

<span></span>

---

## Table of Contents

1. [Parts list](#Parts_list)
1. [Print_bed_3_point_printed_stage_1 assembly](#Print_bed_3_point_printed_stage_1_assembly)
1. [Print_bed_3_point_printed assembly](#Print_bed_3_point_printed_assembly)

<span></span>
[Top](#TOP)

---

## Parts list

| <span style="writing-mode: vertical-rl; text-orientation: mixed;">Print Bed 3 Point Printed Stage 1</span> | <span style="writing-mode: vertical-rl; text-orientation: mixed;">Print Bed 3 Point Printed</span> | <span style="writing-mode: vertical-rl; text-orientation: mixed;">TOTALS</span> |  |
|-----:|-----:|---:|:---|
| | | | **Vitamins** |
| .  | 1  | 1  |  Aluminium tooling plate 120mm x 120mm x 6mm |
| 4  | .  | 4  |  Bolt M3 caphead x  8mm |
| 4  | .  | 4  |  Bolt M3 caphead x 35mm |
| .  | 3  | 3  |  Bolt M3 countersunk x 12mm |
| 4  | .  | 4  |  Bolt M5 countersunk x 12mm |
| .  | 1  | 1  |  Cork underlay 120mm x 120mm x 3mm |
| .  | 1  | 1  |  Heating pad 100mm x 100mm |
| 1  | .  | 1  |  Leadscrew nut 8 x 2 |
| .  | 1  | 1  |  Magnetic base 120mm x 120mm |
| .  | 9  | 9  |  O-ring nitrile 3mm x 2mm |
| 2  | .  | 2  |  SCS12UU bearing block |
| .  | 1  | 1  |  Ziptie 2.5mm x 100mm min length |
|  15  |  17  | 32  | Total vitamins count |
| | | | **3D printed parts** |
| 1  | .  | 1  | Printbed_Frame.stl |
| 1  | .  | 1  | Total 3D printed parts count |

<span></span>
[Top](#TOP)

---

## Print_bed_3_point_printed_stage_1 assembly

### Vitamins

| Qty | Description |
|----:|:---|
| 4 | Bolt M3 caphead x  8mm |
| 4 | Bolt M3 caphead x 35mm |
| 4 | Bolt M5 countersunk x 12mm |
| 1 | Leadscrew nut 8 x 2 |
| 2 | SCS12UU bearing block |

### 3D Printed parts

| 1 x Printbed_Frame.stl |
|----------|
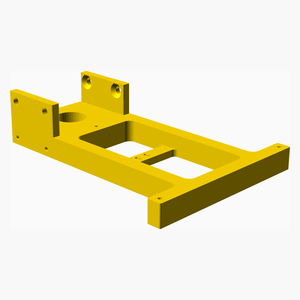
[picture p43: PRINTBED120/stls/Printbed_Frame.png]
Printbed_Frame.stl
|  |

### Assembly instructions

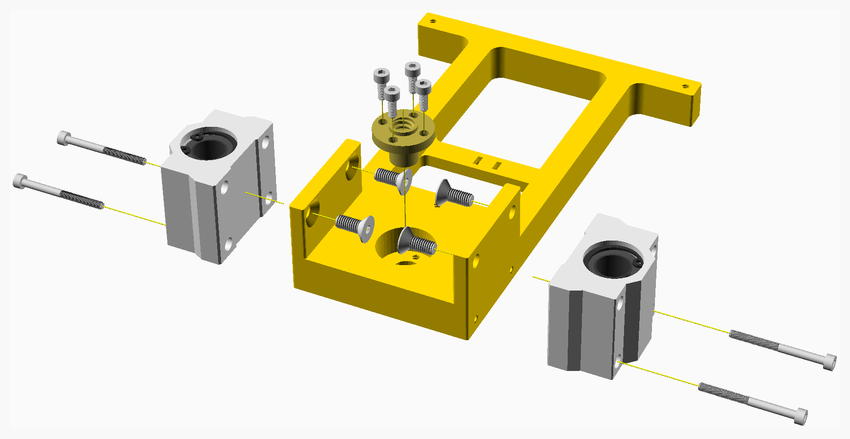
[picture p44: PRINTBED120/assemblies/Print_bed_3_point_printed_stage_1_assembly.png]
Print_bed_3_point_printed_stage_1_assembly


1. Bolt the bearing blocks to the sides of the **Printbed_Frame**.
2. Insert the leadnut and bolt it to the **Printbed_Frame**.

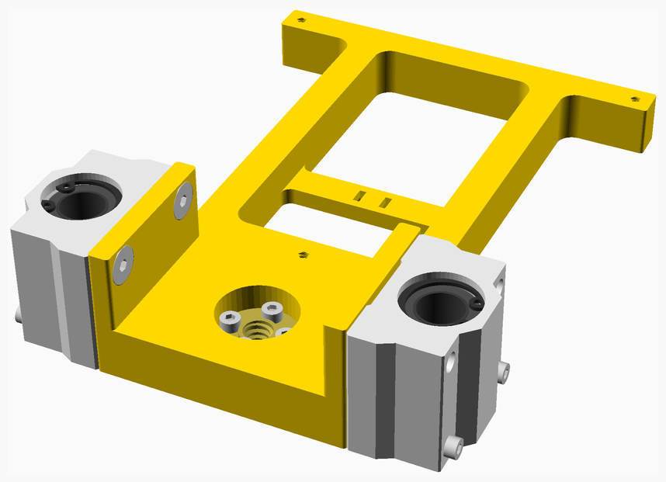
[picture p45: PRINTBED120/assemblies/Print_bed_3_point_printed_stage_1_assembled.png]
Print_bed_3_point_printed_stage_1_assembled


<span></span>
[Top](#TOP)

---

## Print_bed_3_point_printed assembly

### Vitamins

| Qty | Description |
|----:|:---|
| 1 | Aluminium tooling plate 120mm x 120mm x 6mm |
| 3 | Bolt M3 countersunk x 12mm |
| 1 | Cork underlay 120mm x 120mm x 3mm |
| 1 | Heating pad 100mm x 100mm |
| 1 | Magnetic base 120mm x 120mm |
| 9 | O-ring nitrile 3mm x 2mm |
| 1 | Ziptie 2.5mm x 100mm min length |

### Sub-assemblies

| 1 x Print_bed_3_point_printed_stage_1_assembly |
|----------|
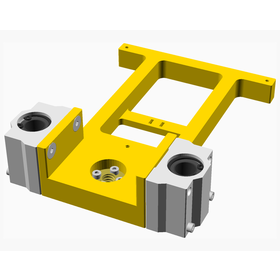
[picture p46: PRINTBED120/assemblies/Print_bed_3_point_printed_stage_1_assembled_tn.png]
Print_bed_3_point_printed_stage_1_assembled
|  |

### Assembly instructions

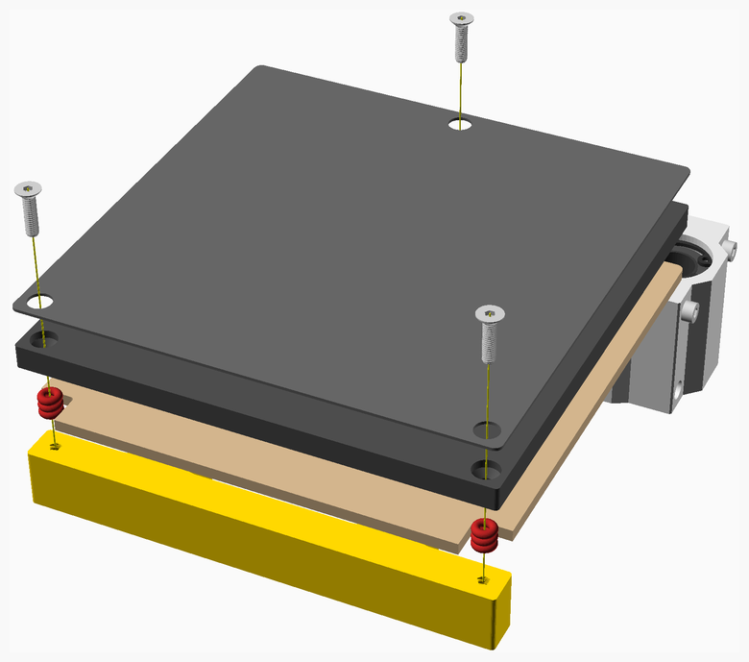
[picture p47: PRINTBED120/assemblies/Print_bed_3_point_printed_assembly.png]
Print_bed_3_point_printed_assembly


1. Prepare the the cork underlay by cutting it to size, making a cutout for the heated bed wiring, and drilling holes
for the bolts.
2. Attach the magnetic base to the top side of the aluminium tooling plate.
3. Attach the heating pad to the bottom side of the tooling plate.
4. Place the cork underlay on the **Printbed_Frame** and place the tooling plate on top.
5. Secure the tooling plate to the **Printbed_Frame**, using the bolts and O-rings. Note that the O-rings allow bed
leveling and help thermally insulate the heated bed from the **Printbed_Frame**.
6. Secure the heating pad wiring to the underside of the **Printbed_Frame** using a cable tie.

Print_bed_3_point_printed_assembled

<span></span>
[Top](#TOP)

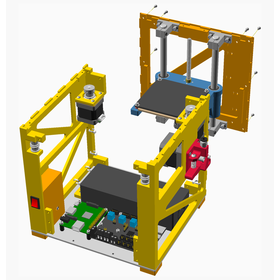
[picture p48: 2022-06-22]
BC200/assemblies/Stage_2_assembly_tn.png

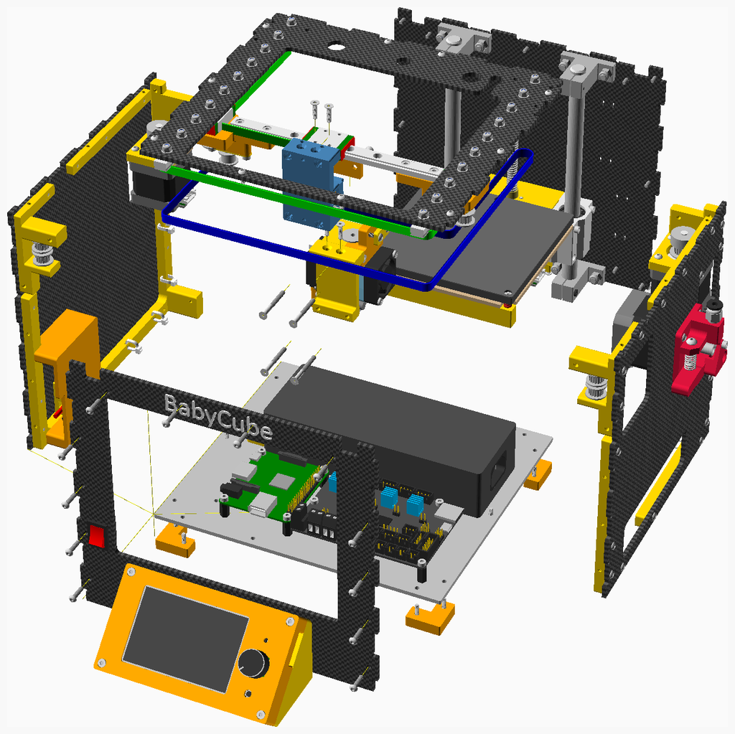
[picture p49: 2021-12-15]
concepts/BC200CF_assembly.png

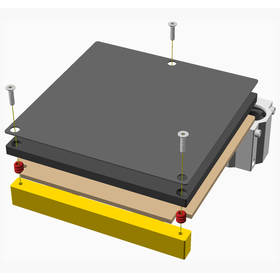
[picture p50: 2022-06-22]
PRINTBED120/assemblies/Print_bed_3_point_printed_assembly_tn.png

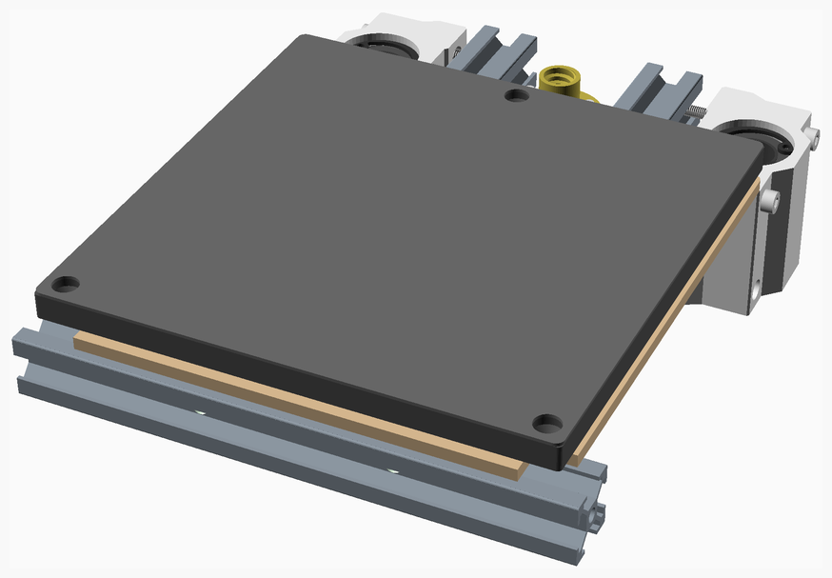
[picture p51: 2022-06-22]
PRINTBED120E15/assemblies/Print_bed_3_point_assembled.png

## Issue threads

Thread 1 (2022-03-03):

Problems when rendering Main.scad

ewasscher, 2022-03-03:
Hi,

I was wondering if you could help me resolve my issue with rendering BabyCube so that I can generate STL's. Maybe I'm doing something wrong/silly. If so please enlighten me.

EDIT: I'm using OpenSCAD version 2021.01

OpenSCAD outputs the following log:

```
Loaded design 'C:/Users/Ewald Wasscher/Downloads/BabyCube/scad/Main.scad'.

Parsing design (AST generation)...
Used file cache size: 96 files
Compiling design (CSG Tree generation)...
[WARNING: Ignoring unknown variable '$target' in file MainAssembly.scad, line 163](https://github.com/martinbudden/BabyCube/issues/163,C:/Users/Ewald%20Wasscher/Downloads/BabyCube/scad/MainAssembly.scad)
[WARNING: Ignoring unknown variable 'NEMA17_40' in file printed/XY_Motors.scad, line 119](https://github.com/martinbudden/BabyCube/issues/119,C:/Users/Ewald%20Wasscher/Downloads/BabyCube/scad/printed/XY_Motors.scad)
[WARNING: Ignoring unknown variable 'NEMA17_40' in file printed/LeftAndRightFaceAssemblies.scad, line 33](https://github.com/martinbudden/BabyCube/issues/33,C:/Users/Ewald%20Wasscher/Downloads/BabyCube/scad/printed/LeftAndRightFaceAssemblies.scad)
[ERROR: Assertion 'isNEMAType(NEMA_type)' failed in file LeftAndRightFaces.scad, line 51](https://github.com/martinbudden/BabyCube/issues/51,C:/Users/Ewald%20Wasscher/Downloads/BabyCube/scad/printed/LeftAndRightFaces.scad)
[TRACE: called by 'assert' in file LeftAndRightFaces.scad, line 51](https://github.com/martinbudden/BabyCube/issues/51,C:/Users/Ewald%20Wasscher/Downloads/BabyCube/scad/printed/LeftAndRightFaces.scad)
[TRACE: called by 'leftFace' in file LeftAndRightFaceAssemblies.scad, line 33](https://github.com/martinbudden/BabyCube/issues/33,C:/Users/Ewald%20Wasscher/Downloads/BabyCube/scad/printed/LeftAndRightFaceAssemblies.scad)
[TRACE: called by 'color' in file LeftAndRightFaceAssemblies.scad, line 32](https://github.com/martinbudden/BabyCube/issues/32,C:/Users/Ewald%20Wasscher/Downloads/BabyCube/scad/printed/LeftAndRightFaceAssemblies.scad)
[TRACE: called by 'children' in file bom.scad, line 146](https://github.com/martinbudden/BabyCube/issues/146,C:/Program%20Files/OpenSCAD/libraries/NopSCADlib/utils/core/bom.scad)
[TRACE: called by 'let' in file bom.scad, line 145](https://github.com/martinbudden/BabyCube/issues/145,C:/Program%20Files/OpenSCAD/libraries/NopSCADlib/utils/core/bom.scad)
[TRACE: called by 'if' in file bom.scad, line 144](https://github.com/martinbudden/BabyCube/issues/144,C:/Program%20Files/OpenSCAD/libraries/NopSCADlib/utils/core/bom.scad)
[TRACE: called by 'if' in file bom.scad, line 143](https://github.com/martinbudden/BabyCube/issues/143,C:/Program%20Files/OpenSCAD/libraries/NopSCADlib/utils/core/bom.scad)
[TRACE: called by 'stl' in file LeftAndRightFaceAssemblies.scad, line 31](https://github.com/martinbudden/BabyCube/issues/31,C:/Users/Ewald%20Wasscher/Downloads/BabyCube/scad/printed/LeftAndRightFaceAssemblies.scad)
[TRACE: called by 'Left_Face_NEMA_17_stl' in file LeftAndRightFaceAssemblies.scad, line 55](https://github.com/martinbudden/BabyCube/issues/55,C:/Users/Ewald%20Wasscher/Downloads/BabyCube/scad/printed/LeftAndRightFaceAssemblies.scad)
[TRACE: called by 'children' in file bom.scad, line 195](https://github.com/martinbudden/BabyCube/issues/195,C:/Program%20Files/OpenSCAD/libraries/NopSCADlib/utils/core/bom.scad)
[TRACE: called by 'let' in file bom.scad, line 194](https://github.com/martinbudden/BabyCube/issues/194,C:/Program%20Files/OpenSCAD/libraries/NopSCADlib/utils/core/bom.scad)
[TRACE: called by 'scale' in file bom.scad, line 193](https://github.com/martinbudden/BabyCube/issues/193,C:/Program%20Files/OpenSCAD/libraries/NopSCADlib/utils/core/bom.scad)
Compiling design (CSG Products generation)...
Geometries in cache: 0
Geometry cache size in bytes: 0
CGAL Polyhedrons in cache: 0
CGAL cache size in bytes: 0
Compiling design (CSG Products normalization)...
Normalized tree has 1 elements!
Compile and preview finished.
Total rendering time: 0:00:18.559

```

ewasscher, 2022-03-04:
To answer my own question: updating NopSCADlib to commit te latest commit in main (738c7914e2e9b61fecdd10b5ffb03ff35f279e12) resolved my issues.

engkon6, 2022-05-05:
Hello @ewasscher ,
Thank you for providing the answer to your question.

You mentioned that you solved this using the latest version of NopSCADlib?
Is there any other steps that are needed to be able to open the file?

Mine showing some error on rounded_rectangle_scad (Assertion... failed) with multiple warnings of "Can't open include file 'target.scad'."

Closed 2022-03-04.

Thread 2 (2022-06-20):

Error when opening Main.scad (LinuxMint 20.2 - OpenSCAD 2021.1)

andimoto, 2022-06-20:
Hi,
this is a nice little printer. I'm thinking about to build one in a few months. Until then I want to get more details and maybe already buy some parts.
I try to open the SCAD model. But unfortunately it does not work and I don't know if I open the correct file.

When I open "Main.scad" I get following error:
`
[WARNING: min() parameter could not be converted in file ../../../../.local/share/OpenSCAD/libraries/NopSCADlib/utils/core/rounded_rectangle.scad, line 25]
[WARNING: undefined operation (undefined / number) in file rounded_rectangle.scad, line 25]
[WARNING: undefined operation (number < undefined) in file rounded_rectangle.scad, line 25]
[ERROR: Assertion '(r < (min(size.x, size.y) / 2))' failed in file rounded_rectangle.scad, line 25](.local/share/OpenSCAD/libraries/NopSCADlib/utils/core/rounded_rectangle.scad)
`
Before this there are a few more Warnings and after this there is a trace back.
I've installed NopSCADlib as described in the installation instructions. I've also tested NopSCADlib, which works fine.

Can you help me here? Is this some known issue or do I need to open something else?

System: Linux Mint 20.2
OpenSCAD 2021.1

Best regards
Andi

andimoto, 2022-09-01:
Hi again,
I've opened Main.scad and got many errors.
Can you please tell me whats the target.scad File? I cannot find it in your Repository or in the NopSCADlib.

Best regards
Andi

engkon6, 2022-09-02:
Hi Andi,
I also have the same error, you can try to follow below tutorial to import and edit the STL files in FreeCAD.
https://youtu.be/dr1qtaURrvI

I hope this can help.

andimoto, 2022-09-02:
Hey,
thanks. I'm more interested  in exploring the model. Thats why I want to load it in OpenSCAD.
Usually I edit STL files in OpenSCAD.

marbocub, 2022-10-28:
Hi, @andimoto

My `target.scad` is below.
~~~
include <config_BC200.scad>
$preview = true;
$target = "BC200";
~~~

andimoto, 2022-10-28:
>

Hey @marbocub ,
thanks.
If I understand this correctly I have to add a target.scad to the folder scad? Is that correct?
I still cannot get a render in OpenSCAD.

marbocub, 2022-10-28:
Hi, @andimoto

Yes, the path is `scad/target.scad`.

andimoto, 2023-01-08:
Sorry for late response. I was able to render the babycube model now. I still had some issues with case-sensitivity. I attach a patch with the files where the includes had case-sensitiv errors and OpenSCAD could not locate the files.

[babycube-patch.txt](https://github.com/martinbudden/BabyCube/files/10368153/babycube-patch.txt)

Closed 2023-01-08.

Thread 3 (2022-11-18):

Which Filament for printing / Contact ?

moelski, 2022-11-18:
Hi Martin,

this is not an issue. It's more two first questions before I start the build :-)

Which Filament did you use for printing the body structure? PLA / ABS / ??
And how much infill did you use?

The other question is to get in contact with you. I would love to make some YT videos with the build of this printer.
Is there any way to get in contact with you on a more direct way like mail / WhatsApp or something like that?
If you like, you can contact me via mail : dominik@drklipper.de

But anyway ... thank you for this awesome project !

Dominik

martinbudden, 2022-11-21:
See https://github.com/martinbudden/BabyCube/tree/main/BC200#tips-for-printing-the-parts - a filament with a high glass transition temperature (ie ABS or PETG) should be used. PLA should not be used, since parts of the printer can get hot enough to cause PLA to soften and bend. Note also the instructions on power management, fans and configuring the printer.

Closed 2024-09-10.

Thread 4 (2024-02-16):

Cannot find Toolhead with PINDA Mount

andimoto, 2024-02-16:
Hi,

I saw some videos from Dr. Klipper on his build of BabyCube. In one of the last Videos he mentioned an updated toolhead with a mount for a "PINDA" probe.
But I cannot find it in the repo. Can you please tell me, where can I find it?

Best regards
Andi

engkon6, 2024-02-16:
It's my mod, you can find it below.

https://www.thingiverse.com/thing:5728648

andimoto, 2024-02-16:
Hey, thanks a lot!

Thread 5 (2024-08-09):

troube viewing .scad files

daduke, 2024-08-09:
Hi Martin,

I just stumbled upon the BabyCube and I think we all know I'll have to build one. I'm still trying to get a good picture of all parts involved (for example, where can I find the cork spacers for the NEMAs), so I tried to open the OpenSCAD files. I installed NopSCADlib, checked out the repo and then tried opening various .scad files, only to be greeted by multiple errors and failed assertions. In the closed issues I found a hint to create the `target.scad` file, but even with this in place I get assertion errors. The only files I could render were the bed variants. I noticed that you're currently reworking .scad files, so maybe that's expected, but I'd be very grateful for some hints on how to get the model opened. MainRB and SB (what's the difference?) do open, but only show one lonely triangle.
OpenSCAD 2021.01 on Fedora 40.

thanks a lot,
-Christian

engkon6, 2024-08-10:
Hi Christian,

For me it's easier just to convert all the STL files to STEP file & create the mockup from there to visualize it.
I follow below tutorial to import and edit the STL files in FreeCAD.
https://youtu.be/dr1qtaURrvI

For the cork spacers, it's installed between the motor & printed frame to insulate the heat from the motor.
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

I could be wrong, but based from the commit description I assume MainRB is for Reversed belt Build and MainSB is for Staged Build.

I hope this can help.

daduke, 2024-08-10:
thanks for your suggestions! I'll look into the STL -> STEP conversion, but I still think it would we nice if the OpenSCAD part were usable...

I realized what the cork spacers are for, but so far I haven't been able to locate a step/stl/dxf/whatever file for them...

thanks again,
-Christian

daduke, 2024-08-12:
ok by increasing the rendering limit in the OpenSCAD settings and commenting out `assert(_useReversedBelts==true || test==true);` in `assemblies/MainAssemblyRB.scad` I got the model to render!

martinbudden, 2024-08-14:
Hi Christian,

sorry the late reply.

I'd hold on a little while if you want to build the BabyCube. It's currently undergoing a fairly major change: I'm changing the belt orientation. The current version is "SB" Standard Belts, the new version is "RB", reversed belts. In the reversed belts version the non-toothed side of the belts passes over (most) of the pulleys, see the illustration below.
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

I've also now pretty well completed the Carbon Fiber version - I plan to build this myself very soon.
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

The new versions have a slightly increased build volume, and also feature exchangable toolheads - I'm planning to support E3DV6, E3D Revo, and DropEffectXG hotends.

martinbudden, 2024-08-14:
And to address your original question, the BabyCube is built using the NopSCAD library build system -  it does take a while to runt the build though. One thing you can do to get a feel for things, is to look at the files in the test directory, or indeed build the tests.

I plan to upload the build instructions for the new variants in about two weeks, so if you can hold on to then, things will be clearer.

daduke, 2024-08-14:
Dear Martin,

thanks for the good news. I'll definitely wait for the new version then. It's a long-term project and I haven't ordered a single part yet. I'll be happy to test the new design and provide feedback.
Do you have any pros/cons for the CF version? We have a workshop on campus that could waterjet the parts for me...

thanks!
-Christian

daduke, 2024-08-14:
great news. I'm not too concerned re: RF blocking - you can always route a thin U.FL coax cable and slap the antenna to the outside.
what thickness of CF plates are you aiming for? I could then use the time to talk to our workshop specialists to see what's feasible.

let's do this!

thanks,
-Christian

martinbudden, 2024-08-14:
3mm thick CF.

I've slightly increased the size, so current planned sizes are:

Front, back, left and right sides: 220x210x3mm
Top: 220x220x3mm

Additionally aluminium base, 220x220x3mm. The only cutting required is drilling holes for mounting the PSU and PCBs, but you might want to investigate having this cut as well.

I'm hoping to increase the build volume from 90x80x60mm (for the original BabyCube) to 99x99x84mm for the CF version., although this varies a bit depending on which hotend used.

martinbudden, 2024-08-14:
One thing you could ask your workshop specialist is about kerf - is there any kerf when cutting with a waterjet? If so, do the .dxf files have to account for this, or does the waterjet control software offset the kerf?

The config files have a parameter for tolerance, currently this is set to 0.05mm for CNC (giving a total tolerance of 0.1mm for fitting the pieces together), but I can adjust this and product a configuration specifically for waterjet.

Also, does the waterjet treat edge cuts and drilling holes differently - will I also need to adjust the diameter of the boltholes for cutting by waterjet? I haven't coded in the ability to do this, but it should be a relatively straightforward change,

daduke, 2024-08-23:
ok I talked to our workshop chief. There is a waterjet cutter at our university, but not in our department (they hope to get one next year), which makes access a bit harder than it could have been. Kerf should be compensated in software, for him the bigger issue was drilling holes - they need to be pre-drilled on a CNC to avoid delamination, and he doesn't like CF in his CNCs since the carbon dust kills his rails. Looking at the many holes on the top plate to hold the linear rails, that might be an issue.
He gave me the contact for a local waterjet specialist shop he had worked with in the past, but this being Switzerland, I'm somewhat hesitant to ask for a quote 🤑
I also tried to find other commercial waterjet services, but at least the usual suspects (JLCPCB, PCBWAY) don't seem to offer it.
How were you going to have your CF cut?

martinbudden, 2024-08-24:
Hi again. Thanks for looking into the waterjet cutting. It looks like it's not really a good option - if you need to use a CNC to drill the holes, then you might as well do the whole thing by CNC. All the faces of the BabyCube have holes drilled, for various purposes, fans, motors, rails and of course to attach the faces to each other.

I'm now at the stage where I can start getting the faces machined. My first step will be to send off a test piece to get check the tolerances for a good fit between the faces.

I've started looking at quotes. There are a couple of small UK CNC workshops that do one-offs and small quantities, so I'll try and get a quote from them this week.

I've also been looking at JLCPCB and PCBWAY. Both do CNC machining, and PCBWAY also does laser cutting. JLCPCB are cheaper, but unfortunately they only do aluminium, polycarbonate and green FR4. PCBWAY do those and also black FR4 and carbon fiber.

I got quotes for cutting out the back face, it's probably fairly representative. All the faces are near enough the same size, but require different amounts of machining. Here are the costs I've got, all for doing the back face (220x210x3mm):

### PCBWAY

#### CNC machining
| Material | Cost |
| --------- | ----- |
| Aluminium | $41.82 |
| Black FR4 | $40.08 |
| Carbon Fiber | $85.84 |
| PolyCarbonate | $39.58 |

#### Laser Cut
| Material | Cost |
| --------- | ----- |
| Aluminium | $33.86 |
| Carbon Fiber | $69.15 |

### JLCPCB
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
daduke, 2024-09-23:
> Hope you had a good holiday.

I did indeed! thanks.

> That fit is bottom side to bottom side of the test piece. I've just check the code, and the bottom side has a tolerance of 0.05mm. That was what I thought it should be, but it's good to have it confirmed.

:+1:

> By the way, what size bit are you using? The dogbone ends have a diameter of 3.5mm, which means you can use either a 3mm bit or a 1/8 inch bit (or smaller). The advantage of 1/8 inch bits is they seem to be more widely available and often cheaper.

I used a 2 mm end mill. I only do metric :smile:

in the next few days I'll try to build an immersion bath so I can mill CF without dying of it.

daduke, 2024-09-28:
first test piece. I am officially thrilled. Dimensional accuracy is ~ 0.02 mm.
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

martinbudden, 2024-09-28:
Looks really nice!

daduke, 2024-10-02:
what kinds of changes do you still see on BC220CF? I've started ordering parts - should I start printing yet?

thanks!

daduke, 2024-10-06:
thanks for the update!

> The BC220CF design is pretty stable now, with no major changes planned. I'll go through it today and double check that and make sure the latest version is up on github.

great, thanks.

> Can you redo the tolerance test, this time with carbon fiber? Just to confirm that the same tolerances are required. CF does not have the same "give" as plywood, so it might need a slightly higher tolerance. Once you have done that I'll regenerate the carbon fiber pieces with the new tolerance if required.

I don't have enough CF sheet on hand right now, and I also noticed that the milled sidewalls have a slight skew, probably from the multiple passes, so I think the requited tolerances will be different for everyone anyway.

I have ordered a couple of 3 mm G10 sheers (I plan to make the 'bottom' out of G10) which should have similar CNC properties, so I guess I can check tolerances with those.

> Note that BabyCube supports interchangeable hotends. I've specified it with the DropEffect XG hotend, since that is one of the most compact available, and a smaller hotend equates to a larger print area. We are talking millimeters here, but in a small printer millimeters count. I am planning to also support the E3D Revo hotend, so if you already have one of those you don't need to order the DropEffect XG. I'll proably also add support for the E3D V6 hotend, but I don't really like that hotend (one of the issues is it has no strain relief on the cables, another is that it is a pain to change the nozzle).

I'll ponder the hotend question when everything else is ready since I'd really like to fit a direct drive extruder (I have a spare Aquarius). A Mini Stealburner mockup doesn't seem to be much bigger than your hotend combo, but we'll see.

I'll also go with a spare Mellow Fly Gemini, but it's tiny enough that this shouldn't cause any issues.

all parts (sans extruder/hotend) should be arriving within the next 10 days. yay!

thanks,
-Christian

martinbudden, 2024-10-06:
>  plan to make the 'bottom' out of G10

I really think you should make the bottom out of aluminium. You can buy sheets of 3mm aluminum quite cheaply and cut to size. So the only work you have to do is to drill the holes. The reason for using aluminium is that it acts as a heatsink - both for the power supply and also the mainboard, if you attach it as indicated in the build instructions.

>  I'd really like to fit a direct drive extruder

Yes, I think there should be room to do this.

daduke, 2024-10-10:
looking at the STLs - don't you want to increase `$fn` in order to get nicer holes?

daduke, 2024-10-16:
back in FR4. So far everything fits amazingly well. Very nice design!
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

martinbudden, 2024-11-04:
Looks really good.

daduke, 2024-11-17:
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

ain't she a beauty

daduke, 2024-12-08:
so my Babycube is as complete as any 3D printer can ever be (one thing left: replace the X linear rail with a Z1 preloaded one), and I created a small picture [gallery](https://daduke.org/pix/cool_stuff/Babycube/) in case you're interested. I'll also attach 3 FreeCAD files I created in the process:

  - a working 1515 bed holder based on your design
  - 1515 endcaps for the front bed extrusion
  - TPU rubber feet

feel free to add them to your repo if you think they might benefit someone.

thanks for a fun project!

[babycube-cad-parts.zip](https://github.com/user-attachments/files/18053145/babycube-cad-parts.zip)

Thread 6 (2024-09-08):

lowercase file name prevents building on case sensitive file systems

daduke, 2024-09-08:
`include <coreXYReversed.scad>` needs to read `include <CoreXYReversed.scad>` in
https://github.com/martinbudden/BabyCube/blob/8fcd44794e0ac9d023c7a8b35ee7d3b93f0f9700/scad/utils/CoreXYBelts.scad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

martinbudden, 2024-09-10:
Fixed in https://github.com/martinbudden/BabyCube/commit/f4ab3ad35dd0231cd2e7106868b4125804431c9b

Closed 2024-09-10.

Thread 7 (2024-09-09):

some STLs missing

daduke, 2024-09-09:
building `BC220CF` fails since `stlimport/DropEffect/*.stl` is missing from the repo

martinbudden, 2024-09-10:
Fixed in https://github.com/martinbudden/BabyCube/commit/7fb169434bc3c5bf4a4601b0b7cae779c60dccdd

Closed 2024-09-10.

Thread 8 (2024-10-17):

BC220CF: part holes don't line up

daduke, 2024-10-17:
`Y_Carriage_Brace_Right_RB` doesn't seem to fit `Y_Carriage_Right_RB` and same with `Y_Carriage_Brace_Left_RB` and `Y_Carriage_Left_RB`. In both cases 2 of the 3 holes line up, but the third is about 1 mm off.

martinbudden, 2024-11-04:
I'll look into it.

daduke, 2024-11-06:
great, thanks. Otherwise my build is almost finished (2 more CF walls missing), so I don't think there'll be more nasty surprises waiting

martinbudden, 2024-11-06:
I've made a fix and uploaded the new STL files. You'll need to reprint both the Y_Carriage and the brace, since the holes have moved on both.

daduke, 2024-11-07:
thanks! Printed my first Marvin today. But I need to do something about the bed, it's very wobbly. Checking your 1515 mod now...
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

Closed 2024-11-19.

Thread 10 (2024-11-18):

question regarding PRINTBED120E15

daduke, 2024-11-18:
in PRINTBED120E15, how is Printbed_Bracket_stl() fixed to the 1515 extrusions? The screws only extend from the bearings to the extrusions.

engkon6, 2024-11-18:
Can try this design for inspiration.

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

https://www.thingiverse.com/thing:5478574

daduke, 2024-11-19:
thank you!

Closed 2024-11-19.

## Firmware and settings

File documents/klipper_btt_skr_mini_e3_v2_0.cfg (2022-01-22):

# This file contains common pin mappings for the BIGTREETECH SKR mini
# E3 v2.0. To use this config, the firmware should be compiled for the
# STM32F103 with a "28KiB bootloader" and USB communication. Also,
# select "Enable extra low-level configuration options" and configure
# "GPIO pins to set at micro-controller startup" to "!PA14".

# The "make flash" command does not work on the SKR mini E3. Instead,
# after running "make", copy the generated "out/klipper.bin" file to a
# file named "firmware.bin" on an SD card and then restart the SKR
# mini E3 with that SD card.

# See https://www.klipper3d.org/Config_Reference.html for a description of parameters.

[mcu]
# Obtain definition by "ls -l /dev/serial/by-id/"
serial: /dev/serial/by-id/usb-Klipper_stm32f103xe_30FFD7054253373814620257-if00

[printer]
kinematics: corexy
max_velocity: 200
max_accel: 3000
max_z_velocity: 25
max_z_accel: 30
square_corner_velocity: 6.0

########################################
#      X/Y/Z Stepper Settings
########################################

# Steppers are set with
# 1. No hold current, since changing motor current can induce motor movement
# 2. spreadCycle mode, so stealthchop_threshold not set
# 3. Interpolation disabled for best possible accuracy, so interpolate set to False

[stepper_x]
step_pin: PB13
dir_pin: PB12
enable_pin: !PB14
microsteps: 16
full_steps_per_rotation: 200 # Set to 400 for 0.9° degree stepper motor, 200 is for 1.8° stepper motors
# Marlin DEFAULT_AXIS_STEPS_PER_UNIT 80
# rotation_distance = <full_steps_per_rotation> * <microsteps> / <steps_per_mm>
# rotation_distance = 200 * 16 / 80;
rotation_distance: 40
#endstop_pin: ^PC0
position_endstop: 0
position_max: 90
# sensorless homing, homing speed should be half rotation_distance
homing_speed: 20
homing_retract_dist: 0
endstop_pin: tmc2209_stepper_x:virtual_endstop

[tmc2209 stepper_x]
uart_pin: PC11
tx_pin: PC10
uart_address: 0
run_current: 0.580
#hold_current: 0.500
interpolate: False
# sensorless homing
diag_pin: ^PC0      # Set to MCU pin connected to TMC DIAG pin
driver_SGTHRS: 255  # 255 is most sensitive value, 0 is least sensitive, suggested value: 55

[stepper_y]
step_pin: PB10
dir_pin: PB2
enable_pin: !PB11
microsteps: 16
full_steps_per_rotation: 200 # Set to 400 for 0.9° degree stepper motor, 200 is for 1.8° stepper motors
# Marlin DEFAULT_AXIS_STEPS_PER_UNIT 80
# rotation_distance = <full_steps_per_rotation> * <microsteps> / <steps_per_mm>
# rotation_distance = 200 * 16 / 80;
rotation_distance: 40
#endstop_pin: ^PC1
position_endstop: 0
position_max: 80
# sensorless homing, homing speed should be half rotation_distance
homing_speed: 20
homing_retract_dist: 0
endstop_pin: tmc2209_stepper_y:virtual_endstop

[tmc2209 stepper_y]
uart_pin: PC11
tx_pin: PC10
uart_address: 2
run_current: 0.580
#hold_current: 0.500
interpolate: False
# sensorless homing
diag_pin: ^PC1      # Set to MCU pin connected to TMC DIAG pin
driver_SGTHRS: 255  # 255 is most sensitive value, 0 is least sensitive, suggested value: 50

[stepper_z]
step_pin: PB0
dir_pin: PC5
enable_pin: !PB1
microsteps: 16
full_steps_per_rotation: 200 # Set to 400 for 0.9° degree stepper motor, 200 is for 1.8° stepper motors
# Marlin DEFAULT_AXIS_STEPS_PER_UNIT 400
# rotation_distance = <full_steps_per_rotation> * <microsteps> / <steps_per_mm>
# rotation_distance = 200 * 16 / 400;
rotation_distance: 8
#endstop_pin: ^PC2
position_endstop: 60
position_max: 60
# sensorless homing, homing speed should be half rotation_distance
homing_speed: 4
homing_retract_dist: 0
endstop_pin: tmc2209_stepper_z:virtual_endstop

[tmc2209 stepper_z]
uart_pin: PC11
tx_pin: PC10
uart_address: 1
run_current: 0.580
#hold_current: 0.500
interpolate: False
# sensorless homing
diag_pin: ^PC2      # Set to MCU pin connected to TMC DIAG pin
driver_SGTHRS: 255  # 255 is most sensitive value, 0 is least sensitive, suggested value: 38

########################################
#   Extruder
########################################

[extruder]
step_pin: PB3
dir_pin: !PB4
enable_pin: !PD2
microsteps: 16
full_steps_per_rotation: 200 # Set to 400 for 0.9° degree stepper motor, 200 is for 1.8° stepper motors
# Marlin DEFAULT_AXIS_STEPS_PER_UNIT 136
# rotation_distance = <full_steps_per_rotation> * <microsteps> / <steps_per_mm>
# rotation_distance = 200 * 16 / 136
rotation_distance: 23.529
nozzle_diameter: 0.400
filament_diameter: 1.750
heater_pin: PC8
sensor_type: EPCOS 100K B57560G104F
sensor_pin: PA0
control: pid
pid_Kp: 22.72
pid_Ki: 1.68
pid_Kd: 76.98
min_temp: 0
max_temp: 250

[tmc2209 extruder]
uart_pin: PC11
tx_pin: PC10
uart_address: 3
run_current: 0.650
#hold_current: 0.500
interpolate: False

########################################
#	Fan Control
########################################

[heater_fan hotend_fan]
# Hotend fan
pin: PC7
kick_start_time: 0.500
heater: extruder
heater_temp: 50.0

[fan]
# Print cooling fan
pin: PC6
kick_start_time: 0.500

########################################
#   Heated Bed
########################################

[heater_bed]
heater_pin: PC9
sensor_type: ATC Semitec 104GT-2
sensor_pin: PC3
control: pid
pid_Kp: 39.41
pid_Ki: 6.38
pid_Kd: 162.212
min_temp: 0
max_temp: 100

########################################
#   Resonance measurement
########################################

# Must set up the RPi as a secondary MCU to do this, see: https://www.klipper3d.org/RPi_microcontroller.html

#[mcu rpi]
#serial: /tmp/klipper_host_mcu

#[adxl345]
#cs_pin: rpi:None

#[resonance_tester]
#accel_chip: adxl345
#probe_points:
#    45,40,15  # 15mm above mid point of bed

########################################
#   Static GPIO output
########################################

[static_digital_output usb_pullup_enable]
pins: !PA14

########################################
#   EXP1 (display) pins
########################################

[board_pins]
aliases:
    # EXP1 header
    EXP1_1=PB5,  EXP1_3=PA9,   EXP1_5=PA10, EXP1_7=PB8,  EXP1_9=<GND>,
    EXP1_2=PA15, EXP1_4=<RST>, EXP1_6=PB9,  EXP1_8=PB15, EXP1_10=<5V>


######################################################################
# 128x64 Full Graphic Creality CR10 / ENDER 3 stockdisplay
######################################################################

# This section is used for a Creality "12864" display with a single
# ribbon cable between the display's EXP3 plug and the
# micro-controller board's EXP1 connector.

# Marlin
# #define CR10_STOCKDISPLAY

[display]
lcd_type: st7920
cs_pin: EXP1_7
sclk_pin: EXP1_6
sid_pin: EXP1_8
encoder_pins: ^EXP1_5, ^EXP1_3
click_pin: ^!EXP1_2

[output_pin beeper]
pin: EXP1_1

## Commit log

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2021-04-27 Added missing XT60 connectors.
    [SwitchShroud.scad]
2021-04-27 Fixed XY_Idler washer positions.
    [XY_IdlerBracket.scad]
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2021-04-28 Improved formatting of assembly instructions.
    [BackFaceAssemblies.scad, Base.scad, MainAssemblies.scad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]
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2021-04-28 Removed BC200 build from .gitignore.
    [BaseAL.dxf]
2021-04-28 Fixed link to horizontal holes.
2021-04-28 Fixed Y_Carriage explostion.
    [TopFaceAssemblies.scad, Y_Carriage.scad]
2021-05-01 Y_Carriage tidy, fairly large scale.
    [BackFace.scad, BackFaceAssemblies.scad, CoreXY.scad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]
2021-05-02 X_Carriage and print head code tidy.
    [MainAssembliesCF.scad, Parameters_CoreXY.scad, Parameters_Main.scad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]
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2021-05-04 Updated box section text.
    [Base.scad]
2021-05-04 Assembly alignment with MaybeCube.
    [PrintheadAssemblies.scad, X_CarriageAssemblies.scad, Y_Carriage.scad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]
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2021-05-05 yRailOffsetXYZ renamed to yRailOffset.
    [BackFace.scad, BackFaceAssemblies.scad, FrontFace.scad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]
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2021-05-09 Updated Bowden offset in extruder.
    [extruder.scad]
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2021-05-09 Fixed spoolHolder explosion.
    [Extras.scad]
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2021-05-14 Added extruder offset test.
    [Extruder.scad]
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2021-05-14 Improved printhead fan duct positioning.
    [Printhead.scad, X_CarriageFanDuct.scad]
2021-05-16 Added right side fan duct.
    [X_CarriageFanDuct.scad]
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2021-05-16 Parameterisde hotEndHolder z offset.
    [Printhead.scad]
2021-05-17 Fixed Extruder Bowden offset.
    [extruder.scad]
2021-05-17 Allow part cooling fan on either side of print head.
    [Printhead.scad, X_CarriageAssemblies.scad, X_CarriageFanDuct.scad]
2021-05-21 Align bolts with MaybeCube.
    [bolts.scad]
2021-05-22 Allowed belt inset to vary with xCarriage type.
    [X_Carriage.scad, X_CarriageAssemblies.scad]
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2021-05-29 Minor improvements to printhead.
    [Printhead.scad]
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2021-05-31 Fixed backface motor position.
    [BackFaceAssemblies.scad]
2021-05-31 Better naming and handling of variant parameters.
    [BackFace.scad, BackFaceAssemblies.scad, Base.scad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]
2021-05-31 Fixed backface z motormount positioning.
    [BackFaceAssemblies.scad]
2021-05-31 Centerd printbed vertically for default position.
    [Parameters_Positions.scad]
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2021-06-01 Fixed to hotend alignment.
    [Printhead.scad, PrintheadAssemblies.scad, X_CarriageAssemblies.scad]
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2021-06-01 Further work on printhead positioning.
    [Printhead.scad, PrintheadAssemblies.scad, X_CarriageAssemblies.scad]
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2021-06-02 Alignment of yCarriage with MaybeCube.
    [Y_Carriage.scad, Y_CarriageAssemblies.scad]
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2021-06-04 Improved 3 point print bed and added assembly instructions.
    [Printbed.scad, Printbed3point.scad, Z_Carriage.scad]
2021-06-04 Changed side bracket M3 boltholes to horizontal.
    [Printbed3point.scad]
2021-06-04 Changed handling of variants in main assemblies.
    [MainAssembly.scad, MainAssemblyCF.scad, MainAssemblyPRINTBED120.scad]
2021-06-04 Changed side bracket M3 boltholes to chamfer only one end..
    [Printbed3point.scad]
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2021-06-04 Updated O-ring and leadnut colours.
    [Printbed.scad, Printbed3point.scad, Z_Carriage.scad]
2021-06-04 Updated PRINTBED120 assembly instructions.
    [MainAssemblyPRINTBED120.scad]
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2021-06-05 Added instructions on configuring the printer.
    [MainAssembly.scad]
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2021-06-05 Renamed Print_head to printhead.
    [MainAssembly.scad, Printhead.scad, PrintheadAssemblies.scad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]
2021-06-05 Added picture for printbed120.
    [MainAssemblyPRINTBED120.scad]
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2021-06-06 Removed ziptie and cutout from left face lower chord.
    [LeftAndRightFaces.scad]
2021-06-06 Fixed horizontal boltholes in reflected form of X_Carriage.
    [X_Carriage.scad]
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2021-06-16 Spell check related corrections.
    [BTT_SKR_V1_4_TURBO.scad, BackFaceAssemblies.scad, Base.scad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]
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2021-06-23 Fixed boltholes on frontLowerChordSKR_1_4.
    [FrontChords.scad]
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2021-07-05 Moved handling of accelerometer into X_Carriage. Reorg of hotend alignment and related.
    [Printhead.scad, PrintheadAssemblies.scad, X_Carriage.scad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]
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2021-07-08 Improved spoolholder and right face for CF variant.
    [Extras.scad, LeftAndRightFaceAssembliesCF.scad, LeftAndRightFaces.scad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]
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2021-07-09 Changed rocker hole to avoid slicer bridging bug.
    [LeftAndRightFaces.scad]
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2021-07-09 Fixed boltHole rotation on XY_MotorMount.
    [XY_MotorMount.scad]
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2021-07-09 Fixed phantom holes in XY motor mount.
    [XY_MotorMount.scad]
2021-07-09 Fixed motor upright length.
    [LeftAndRightFaces.scad]
2021-07-09 Fixed offset in motorCutout.
    [LeftAndRightFaces.scad]
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2021-07-15 Improved X_Carriage sizing and fan positioning for tensioner variant.
    [Printhead.scad, X_Carriage.scad, X_CarriageAssemblies.scad]
2021-07-15 Increased length of blower and fanduct bolt holes.
    [Printhead.scad]
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2021-07-16 Fixed spaces around + and -.
    [BackFace.scad, Base.scad, BoltHoles.scad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]
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2021-07-20 Modified Y_Carriages to allow room for X_Carriage belt attachment.
    [Y_Carriage.scad]
2021-07-20 Refactored X_Carrieages to allow belt attachment for MGN9 carriages.
    [PrintheadAssemblies.scad, X_Carriage.scad, X_CarriageAssemblies.scad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]
2021-07-20 Fixed typo.
    [Y_Carriage.scad]
2021-07-20 Fixed fillet on Y_Carriage.
    [Y_Carriage.scad]
2021-07-20 Full thickness tongue on MGN9C yCarriages for now.
    [Y_Carriage.scad]
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2021-07-27 Parameter fix in call to printBed3pointFrameSideBrackets.
    [Printbed3point.scad]
2021-07-27 Changed bolts and O-rings on printbed for better leveling.
    [Printbed.scad]
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2021-08-02 Improved Y_Carriage clearance for 9C.
    [Y_Carriage.scad]
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2021-08-07 Code tidy and fixed beltattchment bottom size for MGN9C.
    [X_Carriage.scad]
2021-08-07 Fixed to XCarriage belt attachment for MGN9C.
    [Printhead.scad, PrintheadAssemblies.scad, X_CarriageAssemblies.scad]
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2021-08-08 Fixed xCarriageTopHoleOffset.
    [X_Carriage.scad]
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2021-08-21 Fixed camera support on left face.
    [LeftAndRightFaces.scad]
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2021-10-01 Added comment about tolerance.
    [config_BC200CF.scad]
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2021-10-03 Fixed CoreXY test.
    [CoreXY.scad]
2021-10-04 Reduced MGN12 Y_Carriage brace size for more X travel.
    [Y_Carriage.scad]
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2021-10-09 Fixed assembly naming.
    [XY_IdlerBracket.scad, XY_MotorMount.scad]
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2021-10-14 Updated _xMin, _xMax, _zMax. Better parameterised assembly component positions for test.
    [BackFace.scad, BackFaceAssemblies.scad, CoreXY.scad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]
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2021-10-24 Fixed Y_Carriage default insert parameter.
    [Y_Carriage.scad]
2021-10-25 Added cutout to stop interference when inserting Y_Carriage insert.
    [Y_Carriage.scad]
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2021-11-25 Fixed missing semicolon.
    [MainAssembly.scad]
2021-11-25 Fixed X_Carriage sizing and alignment.
    [PrintheadAssemblies.scad, X_Carriage.scad, X_CarriageAssemblies.scad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]
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2021-12-17 Corrected name of blockOffsetX to blockOffsetY.
    [Y_CarriageAssemblies.scad]
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2021-12-21 Fix confusion of extraX and extraOverlap.
    [X_CarriageAssemblies.scad, X_CarriageBeltAttachment.scad]
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2021-12-21 Renaming of X_Carriage sides to belt and hotend sides. Addition of non-NC form.
    [BackFace.scad, Extras.scad, Printhead.scad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]
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2021-12-24 Improved parameterisation of X_Carriage, including better handling of halfCarriage.
    [BackFace.scad, CoreXY.scad, Extras.scad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]
2021-12-24 Fixup after merge.
    [X_Carriage.scad]
2021-12-24 Fixed depth of top belt side connector bolt holes.
    [X_Carriage.scad]
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2021-12-24 Renames to avoid clashes with MaybeCube.
    [CoreXY.scad, LeftAndRightFaceAssemblies.scad, LeftAndRightFaceAssembliesCF.scad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]
2021-12-25 CF build fix.
    [CoreXY.scad, LeftAndRightFaceAssembliesCF.scad, XY_MotorMount.scad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]
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2022-01-24 Fixed include.
    [Y_CarriageAssemblies.scad]
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2022-01-26 Fixed screw size on NIGUY PSU.
    [psus.scad]
2022-01-26 Added facility to cover belts on front face CF.
    [FrontFace.scad]
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2022-01-29 Started adding X_Carriage support for reversed belts.
    [X_CarriageBeltAttachment.scad]
2022-01-29 Further support for reversed belts.
    [Y_Carriage.scad]
2022-01-29 FIrst cut of base cover for CF variant.
    [Base.scad]
2022-01-29 Improved reversed belt support.
    [X_CarriageBeltAttachment.scad]
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2022-01-30 Centered belt tensioner on Z and removed magic numbers.
    [X_CarriageAssemblies.scad, X_CarriageBeltAttachment.scad]
2022-01-30 Simplified positioning of X_Carriage belt attachment and related.
    [X_CarriageAssemblies.scad, X_CarriageBeltAttachment.scad]
2022-01-31 Fixed xCarriageBeltAttachment fillet.
    [X_CarriageBeltAttachment.scad]
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2022-02-23 Bolt etc fixes for non-cnc version.
    [Base.scad]
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2022-03-27 Improved assembly instructions. Emboldened part names. Added CF assembly instructions.
    [BackFaceAssemblies.scad, Base.scad, DisplayHousingAssemblies.scad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]
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2022-06-06 NEMA17 variant fixes.
    [BackFace.scad, LeftAndRightFaceAssemblies.scad, TopFaceAssemblies.scad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]
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2022-06-18 Added missing bolt holes in e front face and back face joiners.
    [LeftAndRightFaceAssembliesCF.scad]
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2022-06-21 Spelling corrections.
    [Parameters_Positions.scad, extruder.scad, global_defs.scad]
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
